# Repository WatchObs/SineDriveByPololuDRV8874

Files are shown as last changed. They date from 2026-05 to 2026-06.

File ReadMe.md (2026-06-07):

Stepper motor driver using two DRV8874 Pololu assemblies for direct and FOC control, AS5047D magnetic position sensing assembly and RS485 assembly. Teensy 4.0 via Arduino IDE to code control of these assemblies. 
The emphasis is control of a Right Ascension axis of an equatorial telescope as the original Makerbase Servo57D did not allow for reducing a rythmic 1+ arcsec variation due to motor pole differences as Makerbase does not provide open sources or access to the processor. In sidereal and pulse tracking mode, direct current control (D axis in D-Q rotor frame of reference) is used as FOC at the 0.25 RPM does not allow sufficient finesse (the stepper is driving a worm directly that drives a 360 tooth gear, 0.25 RPM equates to sidereal), and FOC for slewing.

The board mounted on the back of a Nema 23 stepper for the AS5047D, or if an external (glass type) ABI encoder is used, jumpers provide that programmation.

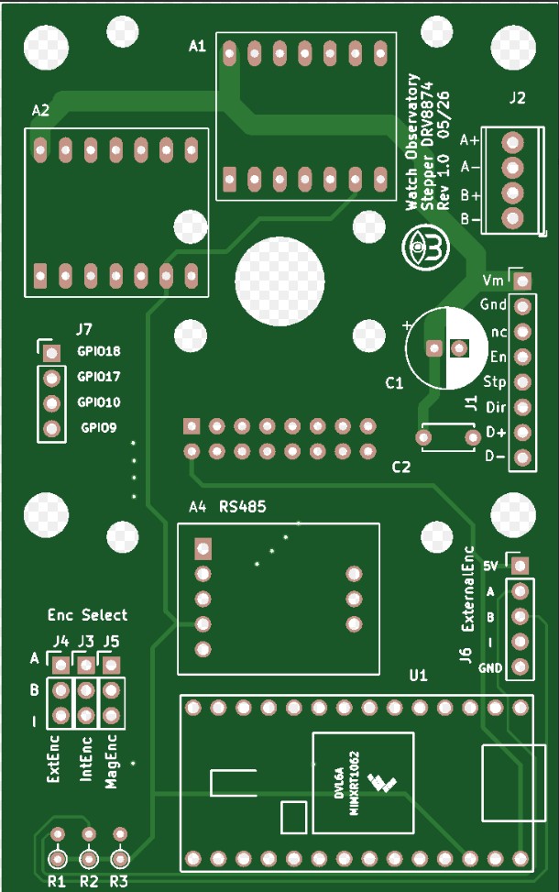
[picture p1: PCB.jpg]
Description

DRV8874Stepper

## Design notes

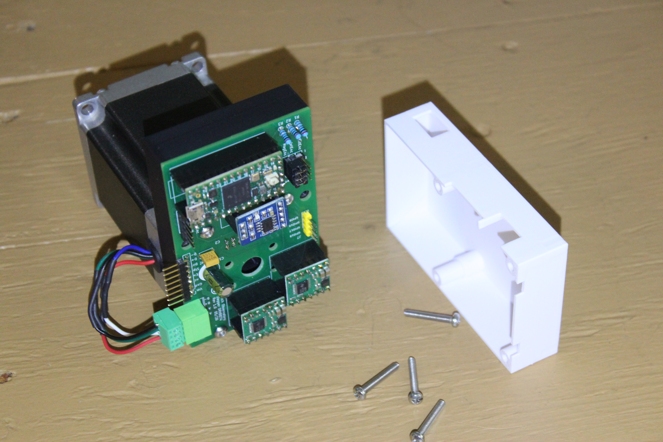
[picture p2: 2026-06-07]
DRV8874Stepper.jpg

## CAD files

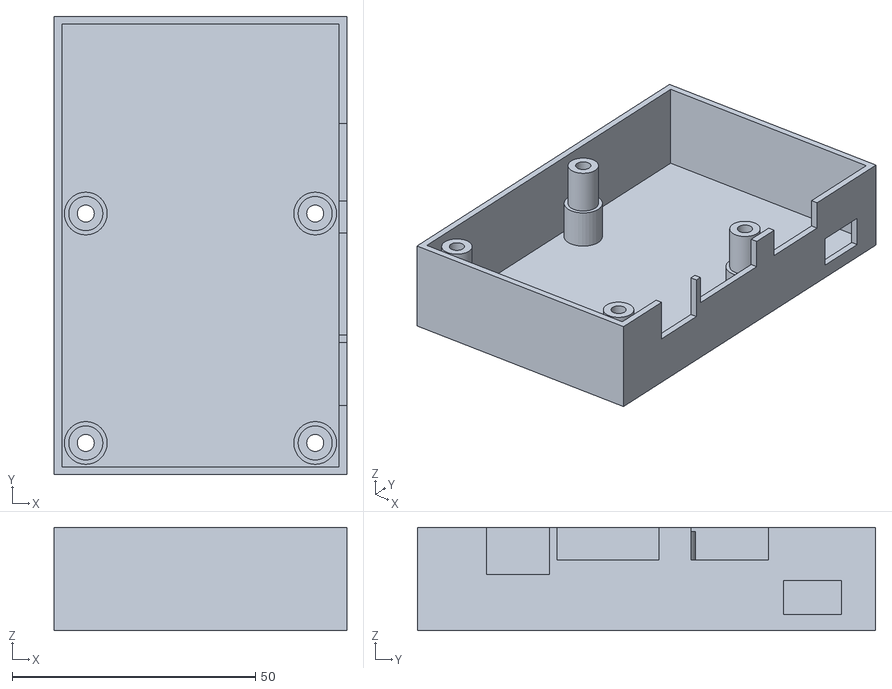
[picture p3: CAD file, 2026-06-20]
Nema23DRV8824 StandAloneCover.stl
60.2 x 94.2 x 21.2

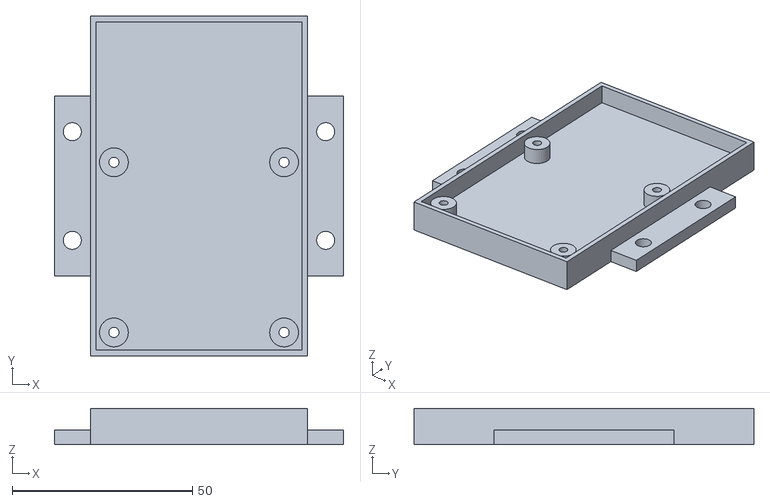
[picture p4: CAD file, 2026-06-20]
Nema23DRV8824 StandAloneBase.stl
80.2 x 94.2 x 10.0

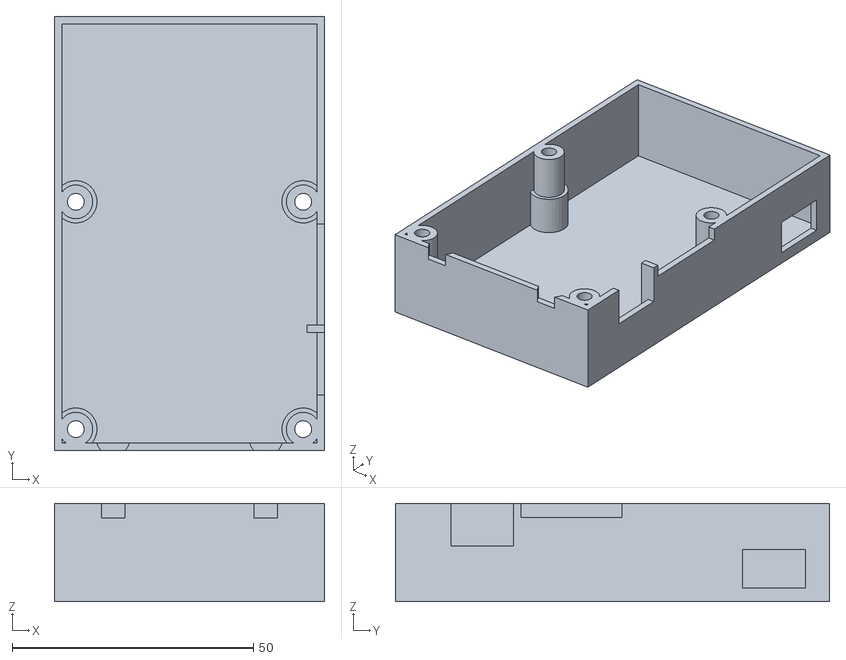
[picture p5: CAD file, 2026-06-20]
Nema23DRV8824.stl
56.0 x 90.0 x 20.4

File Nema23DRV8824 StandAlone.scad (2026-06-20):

//////////////////////////////////////////////////////////////
// Standalone Base + cover 
// DRV8874 based driver - AS5074D or ABI glass encoder
//////////////////////////////////////////////////////////////

$fn = 180;

DoCover = 1;
DoBase  = 0;

// ------------------------------------------------------------
// Motor rear pattern
// ------------------------------------------------------------
bolt_spacing_x   = 31.7;
bolt_spacing_y   = 51.0;
bolt_hole_dia    = 3.5;
nema23_spacing   = 47.14;

// ------------------------------------------------------------
// mainPCBboard standoffs
// ------------------------------------------------------------
mainPCB_w           = nema23_spacing;
mainPCB_h           = nema23_spacing;
mainPCB_standoff_h  = 5; //9.24;
mainPCB_hole_offset = 0;
mainPCBWall         = 1.6;
mainPCBLip          = 0;

post_dia         = 8.0;
post_hole_dia    = 2.8;

// ------------------------------------------------------------
// Base plate geometry
// ------------------------------------------------------------
plate_w          = 56+2*mainPCBWall+1;
plate_h          = 90+2*mainPCBWall+1;
plate_thickness  = 4;

// ------------------------------------------------------------
// Cover geometry
// ------------------------------------------------------------
coverHeight      = 18 + mainPCBWall;
cover_internal_h = 25;
cover_wall       = 2.0;
cover_clearance  = 0.3;
cover_narrow     = 1.0;
cover_offset_x   = plate_w + 20;

//////////////////////////////////////////////////////////////
// Base plate
//////////////////////////////////////////////////////////////
module base_plate() 
{
 difference() 
 {
  // Plate + your tab thickener block
  union() 
  {
   translate([-plate_w/2, -plate_w/2, 0])
    cube([plate_w, plate_h, plate_thickness]);

   // Wall
   translate([0, plate_h/2-plate_w/2, plate_thickness+mainPCB_standoff_h/2])
    difference()
    {
      cube([plate_w,plate_h,mainPCB_standoff_h+mainPCBLip],center=true);
      cube([plate_w-mainPCBWall*2,plate_h-mainPCBWall*2,mainPCB_standoff_h+mainPCBLip],center=true);
    }
  }
 }
  // Mounting tabs
 TabW  = 10;
 TabL  = 50;
 BaseW = plate_w+2*TabW;
 BaseH = plate_h;
 translate([-BaseW/2, plate_h/2-plate_w/2-TabL/2, 0])
  difference()
  {
   cube([BaseW, TabL, plate_thickness]);
   for (y = [-plate_w/4, plate_w/4])
    for (x = [-(BaseW-TabW)/2, (BaseW-TabW)/2])
    {
     translate([x+BaseW/2,TabL/2+y,-5])
      cylinder(h=10,d=5);
    }
  }
}

//////////////////////////////////////////////////////////////
// mainPCBboard standoffs
//////////////////////////////////////////////////////////////
module mainPCBboard_standoffs(drill = 0) 
{
 for (x = [-mainPCB_w/2 + mainPCB_hole_offset, mainPCB_w/2 - mainPCB_hole_offset])
  for (y = [-mainPCB_h/2 + mainPCB_hole_offset, mainPCB_h/2 - mainPCB_hole_offset])
  {
   if (drill)
   {
    translate([x, y, -100])            cylinder(d=post_hole_dia, h=200, $fn=32);
   }
   else
   {
    difference() 
    {
     translate([x, y, plate_thickness]) cylinder(d=post_dia, h=mainPCB_standoff_h, $fn=32);
     translate([x, y, -100])            cylinder(d=post_hole_dia, h=200, $fn=32);
    }
   }
  }
}

module cover() 
{
 postDiaL = 7.0;
 postDiaU = 8.8;
 postDiaIL = 3.5;
 postDiaIU = 6.5;
 postDepthU=coverHeight-10;

 difference() 
 {
  // Plate 
  union() 
  {
   translate([-plate_w/2, -plate_w/2, 0]) cube([plate_w, plate_h, mainPCBWall]);
   
   // Wall
   translate([0, plate_h/2-plate_w/2, coverHeight/2+mainPCBWall-mainPCBLip/2])
   difference()
   {
    cube([plate_w,plate_h,coverHeight-mainPCBLip],center=true);
    cube([plate_w-mainPCBWall*2,plate_h-mainPCBWall*2,coverHeight*1.1-mainPCBLip],center=true);
   }

   // Retainer bolts posts & well (body)
   for (x = [-mainPCB_w/2 + mainPCB_hole_offset, mainPCB_w/2 - mainPCB_hole_offset])
    for (y = [-mainPCB_h/2 + mainPCB_hole_offset, mainPCB_h/2 - mainPCB_hole_offset]) 
    {
     translate([x, y, mainPCBWall/2]) cylinder(d=postDiaL, h=coverHeight);
     translate([x, y, mainPCBWall/2]) cylinder(d=postDiaU, h=postDepthU, $fn=32);
    }
    // Host connector post (strength)
//    translate([plate_w/2-mainPCBWall-2,-plate_w/2+29-0.75,mainPCBWall/2]) 
//     cube([2,1.5,coverHeight-mainPCBLip/2-.2]);
  }

  // Retainer bolts posts & well (holes)
  for (x = [-mainPCB_w/2 + mainPCB_hole_offset, mainPCB_w/2 - mainPCB_hole_offset])
   for (y = [-mainPCB_h/2 + mainPCB_hole_offset, mainPCB_h/2 - mainPCB_hole_offset]) 
   {
    translate([x, y, -5]) cylinder(d=postDiaIL, h=30, $fn=32);
    translate([x, y, 0])  cylinder(d=postDiaIU, h=postDepthU-2, $fn=32);
   }
   translate([0,(2*mainPCBWall-.5),-mainPCBLip/2])
   {
    // Motor connector
    translate([plate_w/2-4,-plate_w/2+11.5,coverHeight+mainPCBWall/2-9+.1])
     cube([6,13,12]);
    // Host connector
    translate([plate_w/2-4,-plate_w/2+26,coverHeight+mainPCBWall/2-6+.1])
     cube([6,21,8]);
    // Encoder connector
    translate([plate_w/2-4,-plate_w/2+26+6+21.5,coverHeight+mainPCBWall/2-6+.1])
     cube([6,16,8]);
    // USB connector
    translate([plate_w/2-4,-plate_w/2+67.5+10/2,coverHeight+mainPCBWall/2-5/2-14.7+.1])
     cube([6,12,7]);
   }
 } // Difference
}

//////////////////////////////////////////////////////////////
// Final assembly
//////////////////////////////////////////////////////////////
union()
{
 if (DoBase)
 {
  difference()
  {
   base_plate();
   mainPCBboard_standoffs(1);
  }
  mainPCBboard_standoffs(0);
 }

 if (DoCover) 
 {
  translate([100,0,0]) cover();
 }
}

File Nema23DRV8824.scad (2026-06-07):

//////////////////////////////////////////////////////////////
// Servo57D Rear Mount Plate + Snap-On Cover (offset)
// DRV8874 based driver board replaces Makerbase driver
// Literal T-cutout + 4  holes + recess for board slide-up
//////////////////////////////////////////////////////////////

$fn = 180;

DoCover = 1;
DoBase  = 0;

// ------------------------------------------------------------
// Motor rear pattern
// ------------------------------------------------------------
bolt_spacing_x   = 31.7;
bolt_spacing_y   = 51.0;
bolt_hole_dia    = 3.5;
nema23_spacing   = 47.14;

// ------------------------------------------------------------
// Base plate geometry
// ------------------------------------------------------------
plate_w          = 56;
plate_h          = 90;
plate_thickness  = 6;

// ------------------------------------------------------------
// Snap-on cover groove
// ------------------------------------------------------------
groove_offset    = 1.5;
groove_height    = 1.5;
groove_depth     = 1.0;

groove_top       = plate_thickness - groove_offset;
groove_bottom    = groove_top - groove_height;

// ------------------------------------------------------------
// Literal T-cutout dimensions
// ------------------------------------------------------------
stem_w = 11;
stem_h = 17;

T_top_w = 24;
T_top_h = 12;

// Side region width (tabs)
side_w = (T_top_w - stem_w) / 2;

// PCB hole spacing
m1_d = 1.8;
hole_dy = 11/2;

// Recess depth for board slide-up
recess_depth = 4.33;

// ------------------------------------------------------------
// mainPCBboard standoffs
// ------------------------------------------------------------
mainPCB_w           = nema23_spacing;
mainPCB_h           = nema23_spacing;
mainPCB_standoff_h  = 9.24;
mainPCB_hole_offset = 0;
mainPCBWall         = 1.6;

post_dia         = 8.0;
post_hole_dia    = 2.8;

// ------------------------------------------------------------
// Cover geometry
// ------------------------------------------------------------
coverHeight = 18+mainPCBWall;
cover_internal_h = 25;
cover_wall       = 2.0;
cover_clearance  = 0.3;
cover_narrow     = 1.0;

rib_height       = groove_height;
rib_depth        = groove_depth * 0.9;

cover_offset_x   = plate_w + 20;

//////////////////////////////////////////////////////////////
// Literal T-shaped through-cut
//////////////////////////////////////////////////////////////
module encoder_T_cutout() {

    translate([-stem_w/2, -stem_h/2, -0.1])
        cube([stem_w, stem_h, plate_thickness + 10]);

    translate([-T_top_w/2, stem_h/2, -0.1])
        cube([T_top_w, T_top_h, plate_thickness + 10]);
}

//////////////////////////////////////////////////////////////
// PCB holes
//////////////////////////////////////////////////////////////
module pcb_bolt_holes() {

    x_left  = -(stem_w/2 + side_w/2);
    x_right =  (stem_w/2 + side_w/2);

    for (x = [x_left, x_right])
    for (y = [-hole_dy, hole_dy])
        translate([x, y, -0.1])
            cylinder(d=m1_d, h=plate_thickness + 10);
}

//////////////////////////////////////////////////////////////
// Recess under side regions
//////////////////////////////////////////////////////////////
module encoder_recess() {

    translate([-(stem_w/2 + side_w), -stem_h/2, 0])
        cube([side_w, stem_h, recess_depth]);

    translate([stem_w/2, -stem_h/2, 0])
        cube([side_w, stem_h, recess_depth]);
}

//////////////////////////////////////////////////////////////
// Triangular groove profile (horizontal wedge)
//////////////////////////////////////////////////////////////
module tri_xz() {
    polygon(points = [
        [0, 0],                 // outer bottom
        [groove_depth, groove_height/2],      // inner bottom
        [0, groove_height]      // vertex inward
    ]);
}

//////////////////////////////////////////////////////////////
// Base plate
//////////////////////////////////////////////////////////////
module base_plate() {
    difference() {

        // Plate + your tab thickener block
        union() {
            translate([0,-1,plate_thickness])
                cube([T_top_w+4, stem_h+2, 4],center=true);

            translate([-plate_w/2, -plate_w/2, 0])
                cube([plate_w, plate_h, plate_thickness]);

            // Wall
            translate([0, plate_h/2-plate_w/2, plate_thickness+mainPCB_standoff_h/2])
            difference()
            {
              cube([plate_w,plate_h,mainPCB_standoff_h],center=true);
              cube([plate_w-mainPCBWall*2,plate_h-mainPCBWall*2,mainPCB_standoff_h],center=true);
            }
        }

        // Motor bolt holes
        for (x = [-bolt_spacing_x/2, bolt_spacing_x/2])
        for (y = [-bolt_spacing_y/2, bolt_spacing_y/2])
            translate([x, y, -0.1])
                cylinder(d=bolt_hole_dia, h=plate_thickness + 10);

        // Literal T-cutout
        encoder_T_cutout();

        // PCB holes
        pcb_bolt_holes();

        // Recess
        encoder_recess();

        // ------------------------------------------------------------
        // Triangular perimeter grooves (correctly rotated)
        // ------------------------------------------------------------

//        // LEFT side (extrude along Y)
//        translate([-plate_w/2, -plate_h/2, groove_bottom])
//            rotate([-90,0,0])
//            linear_extrude(height = plate_h)
//                tri_xz();

//        // RIGHT side (mirror X)
//        translate([plate_w/2, -plate_h/2, groove_bottom])
//            rotate([-90,0,0])
//            mirror([1,0,0])
//                linear_extrude(height = plate_h)
//                    tri_xz();

//        // BOTTOM side (rotate 90°)
//        translate([plate_w/2, -plate_h/2, groove_bottom])
//            rotate([-90,0,90])
//                linear_extrude(height = plate_w)
//                    tri_xz();

//        // TOP side (rotate -90°)
//        translate([-plate_w/2, plate_h/2, groove_bottom])
//            rotate([-90,0,-90])
//                linear_extrude(height = plate_w)
//                    tri_xz();
    }
}

//////////////////////////////////////////////////////////////
// mainPCBboard standoffs
//////////////////////////////////////////////////////////////
module mainPCBboard_standoffs() {

    for (x = [-mainPCB_w/2 + mainPCB_hole_offset, mainPCB_w/2 - mainPCB_hole_offset])
    for (y = [-mainPCB_h/2 + mainPCB_hole_offset, mainPCB_h/2 - mainPCB_hole_offset]) {

        difference() {
            translate([x, y, plate_thickness])
                cylinder(d=post_dia, h=mainPCB_standoff_h, $fn=32);

            translate([x, y, -100])
                cylinder(d=post_hole_dia, h=200, $fn=32);
        }
    }
    
}

//////////////////////////////////////////////////////////////
// Cover (unchanged)
//////////////////////////////////////////////////////////////
module rib_xz() {
    polygon(points = [
        [0, 0],
        [rib_depth, 0],
        [0, rib_height]
    ]);
}

//////////////////////////////////////////////////////////////
// Cover ribs: same isosceles profile + matching rotations
//////////////////////////////////////////////////////////////
module rib_xz() {
    polygon(points = [
        [0, 0],
        [rib_depth, rib_height/2],
        [0, rib_height]
    ]);
}

//////////////////////////////////////////////////////////////
// Cover ribs: same isosceles profile + correct rotations
//////////////////////////////////////////////////////////////
module rib_xz() {
    polygon(points = [
        [0, 0],
        [rib_depth, rib_height/2],
        [0, rib_height]
    ]);
}

module cover() {
postDiaL = 7.0;
postDiaU = 8.8;
postDiaIL = 3.5;
postDiaIU = 6.5;
postDepthU=coverHeight-10;


    difference() {

        // Plate 
        union() 
        {

         translate([-plate_w/2, -plate_w/2, 0]) cube([plate_w, plate_h, mainPCBWall]);

         // Wall
         translate([0, plate_h/2-plate_w/2, coverHeight/2+mainPCBWall/2])
         difference()
         {
           cube([plate_w,plate_h,coverHeight],center=true);
           cube([plate_w-mainPCBWall*2,plate_h-mainPCBWall*2,coverHeight*1.1],center=true);
         }

         // Retainer bolts posts & well (body)
         for (x = [-mainPCB_w/2 + mainPCB_hole_offset, mainPCB_w/2 - mainPCB_hole_offset])
           for (y = [-mainPCB_h/2 + mainPCB_hole_offset, mainPCB_h/2 - mainPCB_hole_offset]) 
           {
             translate([x, y, mainPCBWall/2]) cylinder(d=postDiaL, h=coverHeight,   $fn=32);
             translate([x, y, mainPCBWall/2]) cylinder(d=postDiaU, h=postDepthU, $fn=32);
           }
         // Host connector post (strength)
         translate([plate_w/2-mainPCBWall-2,-plate_w/2+26-1.5,mainPCBWall/2]) cube([2,1.5,coverHeight]);
       }
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

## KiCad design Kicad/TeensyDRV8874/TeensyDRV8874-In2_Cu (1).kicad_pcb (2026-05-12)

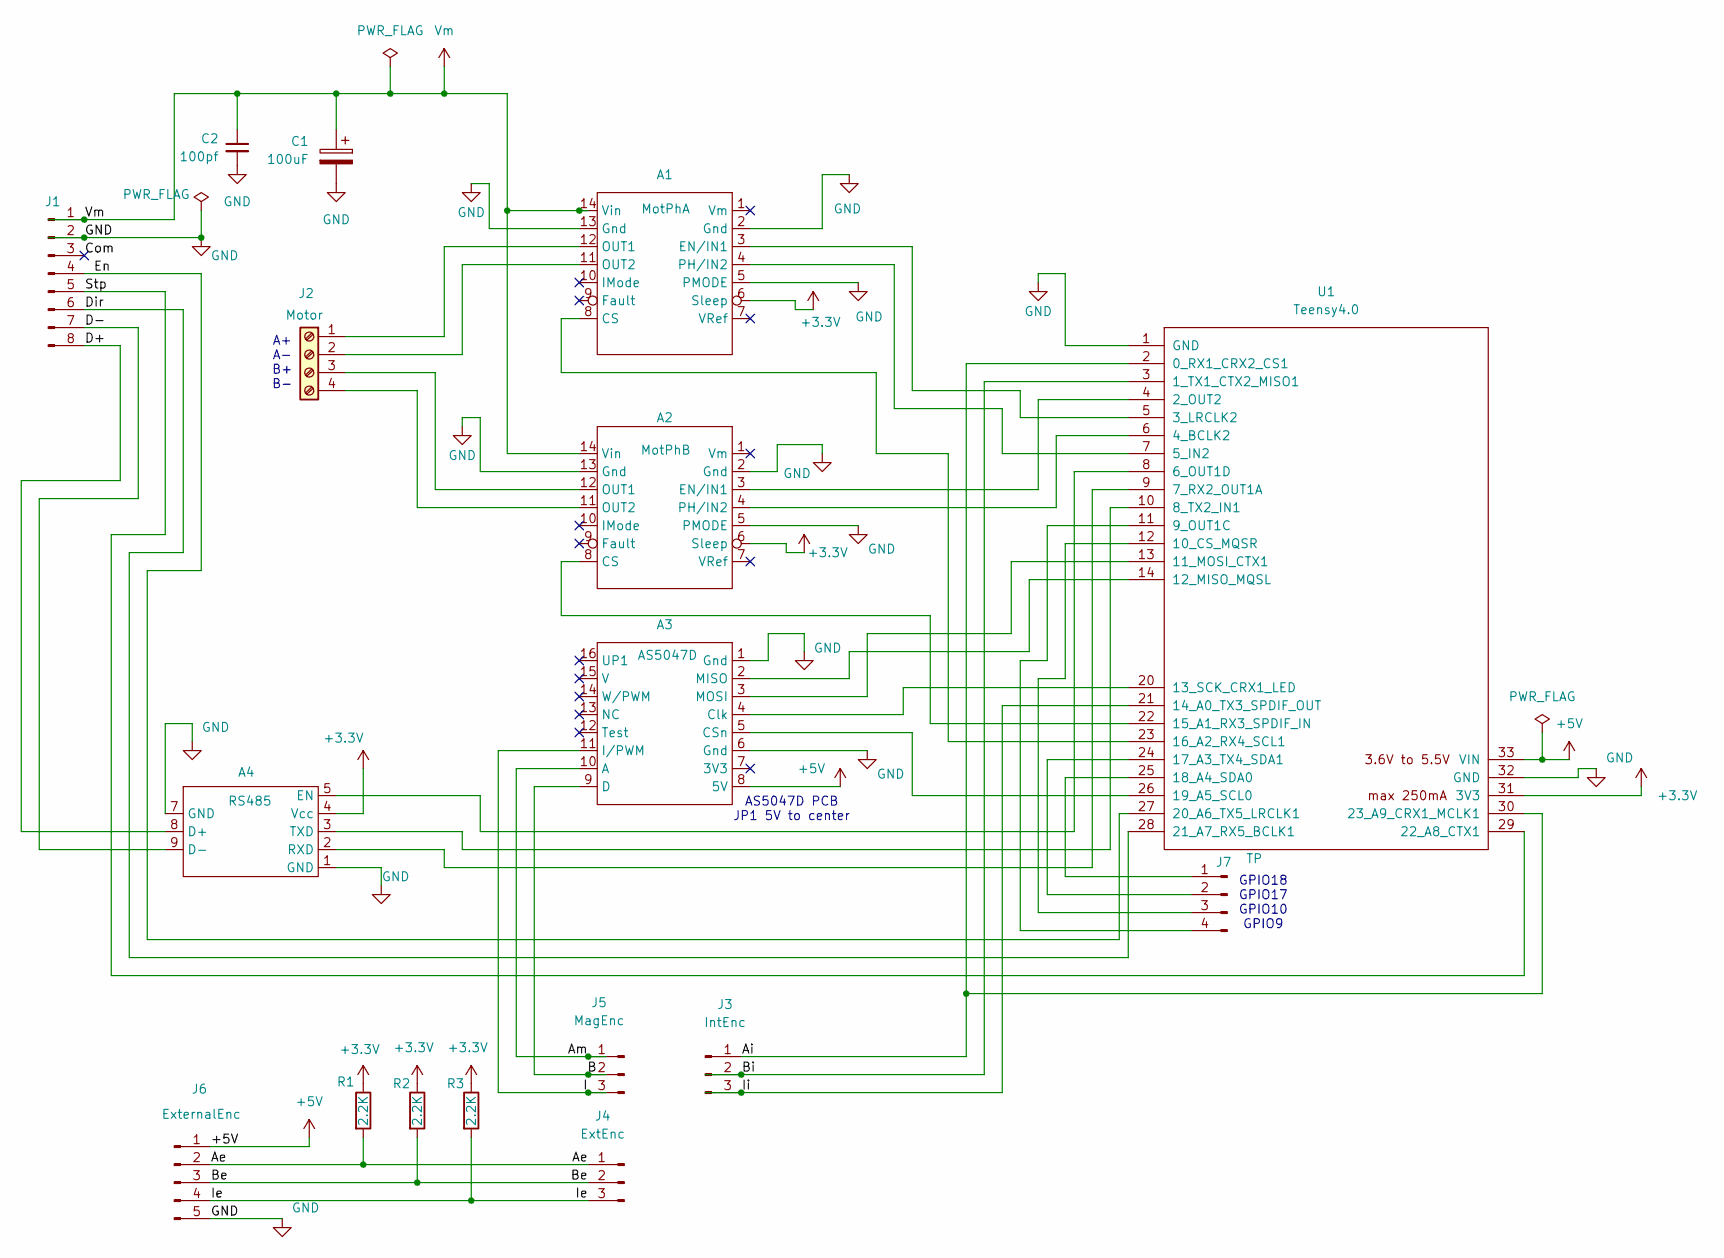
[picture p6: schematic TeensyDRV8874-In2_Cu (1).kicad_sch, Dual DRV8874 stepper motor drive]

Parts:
A1: MotPhA; DRV8874
A2: MotPhB; DRV8874
A3: AS5047D
A4: RS485
C1: 100uF; CP_Radial_D8.0mm_P2.50mm
C2: 100pf; C_Disc_D5.0mm_W2.5mm_P5.00mm
J1: PinHeader_1x08_P2.54mm_Vertical
J2: Motor; TerminalBlock-1x04_P2.54mm_Horizontal
J3: IntEnc; PinHeader_1x03_P2.54mm_Vertical
J4: ExtEnc; PinHeader_1x03_P2.54mm_Vertical
J5: MagEnc; PinHeader_1x03_P2.54mm_Vertical
J6: ExternalEnc; PinHeader_1x05_P2.54mm_Vertical
J7: TP; PinHeader_1x04_P2.54mm_Vertical
R1, R2, R3: 2.2K; R_Axial_DIN0204_L3.6mm_D1.6mm_P2.54mm_Vertical
U1: Teensy4.0; Teensy40

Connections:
+3.3V: A1.6 (Sleep), A2.6 (Sleep), A4.4 (Vcc), R1.1, R2.1, R3.1, U1.31 (3V3)
+5V: A3.8 (5V), J6.1 (+5V), U1.33 (VIN)
/Ae: J4.1 (Ae), J6.2 (Ae), R1.2
/Ai: J3.1 (Ai), U1.2 (0_RX1_CRX2_CS1), U1.30 (23_A9_CRX1_MCLK1)
/Am: A3.10 (A), J5.1 (Am)
/B: A3.9 (D), J5.2 (Bm)
/Be: J4.2 (Be), J6.3 (Be), R2.2
/Bi: J3.2 (Bi), U1.3 (1_TX1_CTX2_MISO1)
/Com: J1.3 (Com)
/D+: A4.8 (D+), J1.8 (D+)
/D-: A4.9 (D-), J1.7 (D-)
/Dir: J1.6 (Dir), U1.28 (21_A7_RX5_BCLK1)
/En: J1.4 (En), U1.27 (20_A6_TX5_LRCLK1)
/I: A3.11 (I/PWM), J5.3 (Im)
/Ie: J4.3 (Ie), J6.4 (Ie), R3.2
/Ii: J3.3 (Ii), U1.21 (14_A0_TX3_SPDIF_OUT)
/Stp: J1.5 (Stp), U1.29 (22_A8_CTX1)
GND: A1.2 (Gnd), A1.5 (PMODE), A1.13 (Gnd), A2.2 (Gnd), A2.5 (PMODE), A2.13 (Gnd), A3.1 (Gnd), A3.6 (Gnd), A4.1 (GND), A4.7 (GND), C1.2, C2.2, J1.2 (GND), J6.5 (GND), U1.1 (GND), U1.32 (GND)
unnamed: A1.8 (CS), U1.23 (16_A2_RX4_SCL1)
unnamed: A1.3 (EN/IN1), U1.5 (3_LRCLK2)
unnamed: A1.12 (OUT1), J2.1 (A+)
unnamed: A1.11 (OUT2), J2.2 (A-)
unnamed: A1.4 (PH/IN2), U1.7 (5_IN2)
unnamed: A2.8 (CS), U1.22 (15_A1_RX3_SPDIF_IN)
unnamed: A2.3 (EN/IN1), U1.4 (2_OUT2)
unnamed: A2.12 (OUT1), J2.3 (B+)
unnamed: A2.11 (OUT2), J2.4 (B-)
unnamed: A2.4 (PH/IN2), U1.6 (4_BCLK2)
unnamed: A3.5 (CSn), U1.26 (19_A5_SCL0)
unnamed: A3.4 (Clk), U1.20 (13_SCK_CRX1_LED)
unnamed: A3.2 (MISO), U1.14 (12_MISO_MQSL)
unnamed: A3.3 (MOSI), U1.13 (11_MOSI_CTX1)
unnamed: A4.5 (EN), U1.8 (6_OUT1D)
unnamed: A4.2 (RXD), U1.9 (7_RX2_OUT1A)
unnamed: A4.3 (TXD), U1.10 (8_TX2_IN1)
unnamed: J7.1, U1.25 (18_A4_SDA0)
unnamed: J7.2, U1.24 (17_A3_TX4_SDA1)
unnamed: J7.3, U1.12 (10_CS_MQSR)
unnamed: J7.4, U1.11 (9_OUT1C)
Vm: A1.14 (Vin), A2.14 (Vin), C1.1, C2.1, J1.1 (+15V)

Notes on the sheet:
GPIO18 GPIO17 GPIO10 GPIO9
AS5047D PCB JP1 5V to center
A+ A- B+ B-

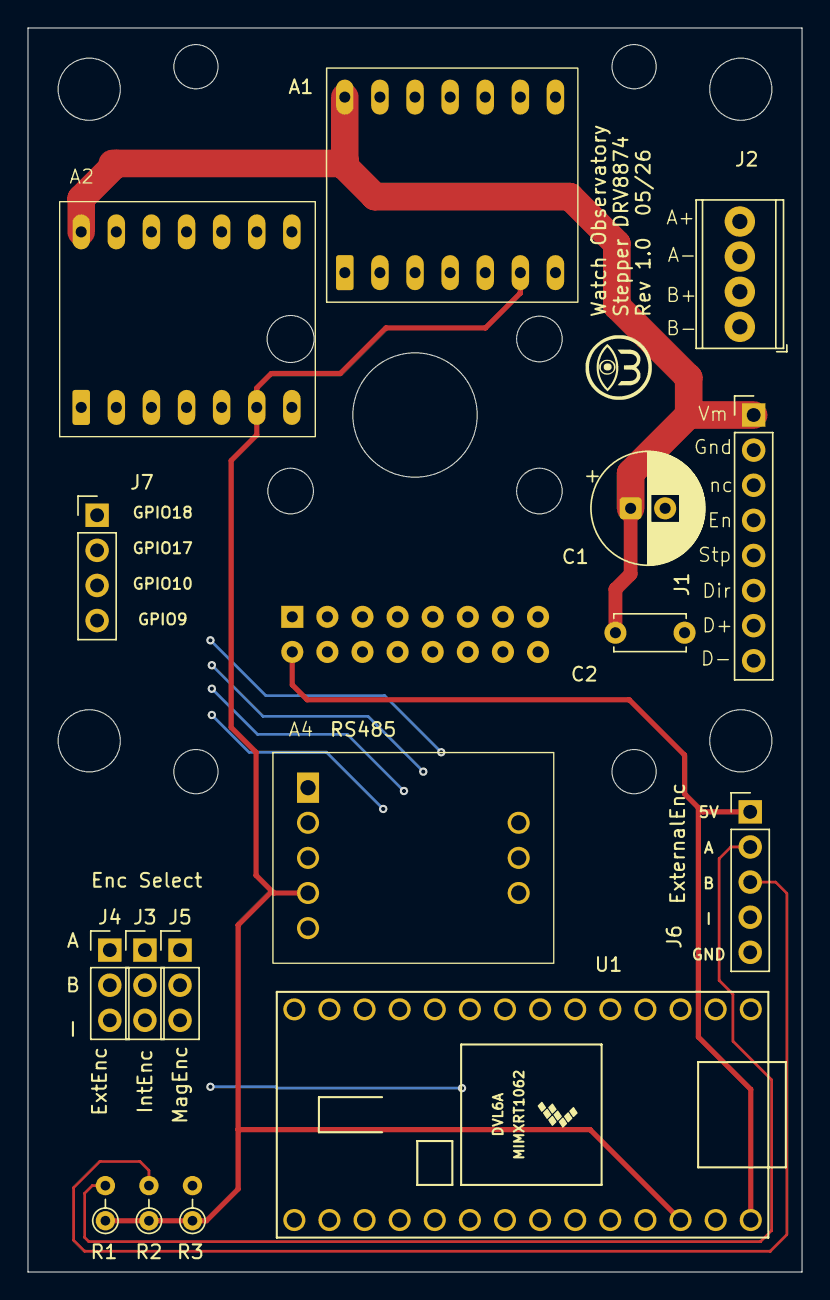
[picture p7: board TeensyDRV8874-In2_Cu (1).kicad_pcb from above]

Board: 4 copper layers, 56.0 x 90.0 mm, 18 parts (1 on the bottom side), 39 nets.

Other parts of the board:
Nema23: MountingHole_4.5mm

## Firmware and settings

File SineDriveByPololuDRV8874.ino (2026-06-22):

/*
  Sinusoidal micro stepper with loss-of-pulses safety
  - External STEP on pin 21 used only for measurement (freq)
  - ISR integrates published host rate (indices per ISR) into a float phase accumulator
  - If no STEP edges seen for LOSS_TIMEOUT_MS, published rate is forced to zero
*/

#include <Arduino.h>
#include <stdint.h>
#include <math.h>
#include <FreqMeasureMulti.h>
#include <Encoder.h>
#include <SPI.h>

// --- Host step loss timeout ---
const uint32_t LOSS_TIMEOUT_MS = 500;   // adjust as needed
volatile uint32_t lastHostStepTime = 0;
volatile bool hostTimedOut = false;

volatile float fMax = 0.f;
volatile float fMin = 0.f;

// Pins
const int PIN_A_PH         = 5;   // Phase (direction) for winding A
const int PIN_A_EN         = 3;   // Enable (PWM) for winding A
const int PIN_B_PH         = 4;   // Phase (direction) for winding B
const int PIN_B_EN         = 2;   // Enable (PWM) for winding B
const int PIN_CS_A         = 16;  // DRV8874 CS for winding A - current sensing
const int PIN_CS_B         = 15;  // DRV8874 CS for winding B - current sensing

const int PIN_ENC_A        = 0;   // Encoder Quadrature A
const int PIN_ENC_B        = 1;   // Encoder Quadrature B
const int PIN_ENC_IDX      = 14;  // Encoder Index (Z)  [was 12 with disk encoder]
const int PIN_ENC_RATE     = 23;  // Measure encoder pulse rate (phase A) - pairs with 22
const int PIN_ENC_MOSI     = 11;  // Encoder comm (SPI0 - define here only to lock pin from being used)
const int PIN_ENC_MISO     = 12;  // Encoder comm (SPI0 - define here only to lock pin from being used)
const int PIN_ENC_SCK      = 13;  // Encoder comm (SPI0 - define here only to lock pin from being used)

const int PIN_HOST_ENABLE  = 20;  // Host motor enable DIP
const int PIN_HOST_DIR     = 21;  // Host motor direction DIP
const int PIN_HOST_RATE    = 22;  // Host requested rate (freq) - pairs with 23

const int PIN_RX2          = 7;   // RS485 receive comm with host
const int PIN_TX2          = 8;   // RS485 transmit comm with host
const int PIN_DE_RE        = 6;   // RS485 bus enable

const int PIN_ISR_TOGGLE   = 10;  // Debug - ISR active signal (monitor CPU usage by ISR)
const int PIN_RATE_PWM     = 9;   // Debug - local motor rate
const int PIN_LED          = 13;  // On-board LED (also SPI SCK)

const int PIN_ENC_CS       = 19;  // AS5047D chip select (CSn)

const uint32_t RS485_BAUD = 115200; // RS485 host comm baud rate

// Waveform / motor geometry
const int   BPWM_FREQ       = 25000;          // PWM frequency for DRV8874 driver
const uint32_t uStepPerTurn = 51200;          // Microsteps per revolution
const float maxFreq         = uStepPerTurn*5; // Maximum frequency (set according P/S & stepper specs)
const float transFreqHz     = uStepPerTurn/2; // Frequency for drive mode transition
const int   PWM_BITS        = 12;             // PWM resolution
const float PWM_MAG         = (float)(pow(2, PWM_BITS)-0); // PWM magnitude
#define MAG_CYCLES_PER_REV  50                // Electrical cycles per mechanical revolution
#define CAL_CNT MAG_CYCLES_PER_REV            // AS5074D calibration indexes

const uint32_t RATE_PWM_FREQ_HZ = uStepPerTurn*5; // Debug - FOR TESTING

// ISR timing
const uint32_t ISR_FREQ_HZ   = 25000UL;                 // ISR ticks per second
const uint32_t ISR_PERIOD_US = 1000000UL / ISR_FREQ_HZ; // dt in uSec
const float    ISR_DT        = 1.f/(float)ISR_FREQ_HZ;  // dt in sec
volatile float isrTmUs       = 0.f;                     // ISR run time micro seconds

// Host rate steps/sec conversion to magnetic phase
const float rateToDeg  = 360.f/(float)uStepPerTurn;

// ADC
const int ADC_BITS = 12;

// AS5047D uses SPI MODE1, up to 10 MHz
SPISettings encSPI(10000000, MSBFIRST, SPI_MODE1);

// --- Shared state (volatile for ISR/main) ---
volatile double cmdDeg        = 0.0f;   // Commanded shaft angle (degrees) fine resolution due to ISR dt integration at low slew rates
volatile float  phaseAdv      = 0.0f;   // Phase advance
volatile float  pE            = 0.0f;   // Position error
volatile float  pEI           = 0.0f;   // Position error integration
volatile float  vE            = 0.0f;   // Velocity error
volatile float  vEI           = 0.0f;   // Velocity error integration
volatile float  vdE           = 0.0f;   // I2V D axis error
volatile float  vdEI          = 0.0f;   // I2V D axis error integration
volatile float  vqE           = 0.0f;   // I2V Q axis error
volatile float  vqEI          = 0.0f;   // I2V Q axis error integration
volatile float  dirSign       = 1;      // +1 CW, -1 CCW
volatile int8_t enableDrv     = HIGH;   // Drive enable
volatile int    releaseForUse = 0;      // Stepper released for normal drive
volatile float  freqMeasureHz = 0.f;    // Host step frequency

volatile int   isrCount = 0;

FreqMeasureMulti FreqMeasure1;          // Measure host step rate
FreqMeasureMulti FreqMeasure2;          // Measure encoder phase A rate

// Slew-limited output frequency for phase integration
volatile float slewFreqHz = 0.f;        // deg/sec
const float SLEW_RATE_HZ_PER_ISR = (float)uStepPerTurn * 5.f / (float)ISR_FREQ_HZ;

// Driver motor currents
#define MAX_CURR       2.1f  // Max current limit DRV8824 (continuous)
#define SUP_VOLT      15.f   // Supply voltage
#define PHASE_ADV      5.f   // Phase advance per 360 deg/sec motor velocity
#define PHASE_ADV_MAX 30.f   // Maximum permissible phase advance
#define DIRECT_CURR   1.5f   // Direct mode target current (d axis)
// 15V supply, 4.8 mH, 1.13 ohms, 23HS30-2804D StepperOnline nema 23
// 15V supply, 3.0 mH, 1.00 ohms, 57BYGH633 Servo57D stepper Nema 23
#define V_KP          0.5f   // Proportional voltage gain (normalized)
#define V_KI          2.0f   // Integral voltage gain (normalized)
#define SERVO_KP      0.7f   // Position error gain (was 2 with external 00ppr encoder)
#define SERVO_KPI     0.2f   // Integrated position error gain
#define SERVO_KV    0.002f   // Velocity error gain
#define SERVO_KVI    0.01f   // Integrated velocity error gain
const    float convCS = (3.3f/(float)pow(2,ADC_BITS)) * (1.0f/1.1f); // CS scaling: 1.1V/A
volatile float Ia    = 0.f;  // Motor coil current A
volatile float Ib    = 0.f;  // Motor coil current B
volatile float Id    = 0.f;  // Rotor frame current - D axis
volatile float Iq    = 0.f;  // Rotor frame current - Q axis
volatile float IqDem = 0.f;  // Rotor frame demanded current - Q axis
volatile float IaPol = 1.f;  // Polarity of current A
volatile float IbPol = 1.f;  // Polarity of current B
volatile float Va    = 0.f;  // Duty cycle phase A
volatile float Vb    = 0.f;  // Duty cycle phase 
volatile float Vd    = 0.f;  // Duty cycle D 
volatile float Vq    = 0.f;  // Duty cycle Q
volatile float IdReq = DIRECT_CURR; // Rotor frame 0 D axis requested current

#define USE_EXT_ENC  1  // Use external encoder (ABI) otherwise AS5074D SPI magnetic position 14 bits

#if (USE_EXT_ENC)
#define ENC_REZ             2500  // Encoder counts per turn either phase - glass external encoder
#define CAL_ENC_REZ (ENC_REZ *4)  // Encoder rez for calibration
#else
#define ENC_REZ              512  // Encoder counts per turn either phase - AS5074D ABI default boot up value (and max)
#define CAL_ENC_REZ    (1 << 14)  // Encoder rez for calibration 
#endif
#define ENC_QUAD_REZ (ENC_REZ * 4)// Encoder quadrature counts per turn
#define CAL_NONE               0  // AS5074D calibration not done
#define CAL_LEARN              1  // AS5074D calibration learn (sweeping)
#define CAL_DONE               2  // AS5074D calibration learn completed
#define CAL_VALID              3  // AS5074D calibration valid
Encoder motorEncoder(PIN_ENC_A, PIN_ENC_B);
volatile float  motDeg    = 0.f;  // Motor shaft position in degrees
volatile uint16_t magStat = 0;    // AS5074D angle error status bit
volatile uint16_t magRaw  = 0;    // AS5074D 14 bit position + error + parity
volatile uint16_t magDec  = 0;    // AS5074D 14 bit position
volatile float magDeg     = 0;    // AS5074D linearized degrees
volatile float encVel2     = 0.f;  // AS5074D velocity in deg/sec
volatile int   encCalRun  = CAL_NONE; // AS5074D calibration run
volatile int   poleNum    = 0;    // AS5047D calibration run pole number
volatile bool  magBusy    = false;// AS5074D API busy
volatile long  encCnt     = 0;    // Encoder quadrature counts
volatile int   encIndex   = -1;   // Encoder index detection count
volatile float encDeg     = 0.f;  // Encoder shaft angle in degrees
volatile float encOffset  = 0.f;  // Encoder offset (to magnetic cycle)
volatile float encVel     = 0.f;  // Encoder computed velocity from phase A period
volatile float commNrm    = 0.f;  // Commutation angle (normalized)
volatile float commRad    = 0.f;  // Commutation angle (radians)
volatile float magRad     = 0.f;  // Resolved magnetic angle (radians)
volatile float slewRate   = 0.f;  // Motor slew rate deg/sec shaft angle
volatile float motorVel   = 0.f;  // Motor velocity

struct CalibPoint 
{
  int16_t  dec;  // raw encoder position (counts)
  float    deg;  // true mechanical angle (degrees)
  float    m;    // slope
  int      cal;  // calibration flag
};
CalibPoint encCal[CAL_CNT];

#define limit0(A)     (((A)>1.f)   ? 1.f         : (((A)<-1.f)   ? -1.f        : (A)))
#define limit1(A,B)   (((A)<(-B))  ? (-B)        : (((A)> (B))   ?  (B)        : (A)))
#define limit2(A,B,C) (((A)<(B))   ? (B)         : (((A)> (C))   ?  (C)        : (A)))
#define limit180(A)   (((A)>=180.f)? ((A)-360.f) : (((A)<-180.f) ? ((A)+360.f) : (A)))
#define limit360(A)   (((A)>=360.f)? ((A)-360.f) : (((A)<0.f)    ? ((A)+360.f) : (A)))
#define limit360D(A)  (((A)>=360.) ? ((A)-360.)  : (((A)<0.)     ? ((A)+360.)  : (A)))
#define db(A,B)       (((A)>(B))?((A)-(B)):(((A)<-(B))?((A)+(B)):0))
#define hys(A,B,C)    (((A-B)>(C))?(A-C):(((A-B)<-C)?(A+C):B))
#define sign(A)       (((A) < 0)   ? -1   : 1)
#define signf(A)      (((A) < 0.f) ? -1.f : 1.f)

// ---------------------------------------------------------------------------
// Command defines (with parity pre-applied)
// ---------------------------------------------------------------------------
#define CMD_ANGLECOM   0xFFFF // ANGLECOM (0xFFFF) → returns: [15]=parity, [14]=error, [13:0]=angle
#define CMD_ERRFL      0x4001 // read + parity - ERRFL register (0x0001)
#define CMD_STATUS     0x7FFD // read + parity - STATUS register (0x3FFD)
#define CMD_DIAG       0x7FFC // read + parity - DIAAGC register (0x3FFC)
#define AS5047_ANGLE14      0 // 14 bit angle only
#define AS5047_RAW          1 // raw 16‑bit frame (parity + error + angle)
#define AS5047_ERRFL        2 // error flags
#define AS5047_STATUS       3 // status register
#define AS5047_DIAG         4 // diagnostics (AGC + MAG + flags)

uint16_t AS5047_Read(uint16_t what)
{
  uint16_t raw;

  auto spi_xfer = [&](uint16_t cmd) -> uint16_t 
  {
    uint16_t res;
    digitalWrite(PIN_ENC_CS, LOW);
    SPI.beginTransaction(encSPI);
    res = SPI.transfer16(cmd);
    SPI.endTransaction();
    digitalWrite(PIN_ENC_CS, HIGH);
    return res;
  };

  switch (what)
  {
    case AS5047_ANGLE14:
      // Clean 14-bit angle (0–16383)
      raw = spi_xfer(CMD_ANGLECOM);
      return raw & 0x3FFF;

    case AS5047_RAW:
      // Full 16-bit frame:
      // bit15 = parity, bit14 = error, bits13:0 = angle
      return spi_xfer(CMD_ANGLECOM);

    case AS5047_ERRFL:
      // ERRFL bits:
      // bit0 = framing error
      // bit1 = invalid command
      // bit2 = parity error
      // bit3 = diagnostic error
      // bit4 = magnet too strong
      // bit5 = magnet too weak
      // bit6 = CORDIC overflow
      return spi_xfer(CMD_ERRFL);
  
    case AS5047_STATUS:
      // STATUS bits:
      // bit3 = MAGH (mag too strong)
      // bit4 = MAGL (mag too weak)
      // bit5 = COF (CORDIC overflow)
      // bit6 = OCF (offset compensation finished)
      // bit7 = AGC overflow
          return spi_xfer(CMD_STATUS);
    
    case AS5047_DIAG:
      // DIAAGC bits:
      // bits 7:0  = AGC value
      // bits 13:8 = MAG value
      // bit14     = LF  (loss of tracking)
      // bit15     = COF (CORDIC overflow)
      return spi_xfer(CMD_DIAG);
    
    default:
      return 0;
  }
}

void DRV8874(float val, int PIN_PH, int PIN_EN)
{
  digitalWrite(PIN_PH, (val < 0.f) ? LOW : HIGH); // Reverse or Forward
  analogWrite(PIN_EN, (uint16_t)fabsf(val * PWM_MAG));
}

void encoderIndexISR() 
{
  if (USE_EXT_ENC || !releaseForUse)  // reset encoder per cycle causes tiny audible glitch with AS5074D ABI
  {                                    // but not with external encoder
    motorEncoder.write(0); // Zero the encoder position on index pulse
    encCnt = 0;            // Zero the tracked position
    encIndex++;
  }
}
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
void loop() 
{
  static int      operStep     = 0;
  static uint32_t magPoleTime  = 0;
  static uint32_t lastDebugMs  = 0;

  switch (operStep)
  {
    case 0:
      if (USE_EXT_ENC)      
        Serial.println("Position from external encoder");
      else
        Serial.println("Position from AS5074D");

      Serial.print("ABI resolution ");
      Serial.println(ENC_REZ);
      Serial.print("ABI quad resolution ");
      Serial.println(ENC_QUAD_REZ);
      Serial.print("Calibration resolution ");
      Serial.println(CAL_ENC_REZ);

      Serial.println("Index search");
      releaseForUse = 0;
      enableDrv     = HIGH;
      dirSign       = 1.0f;
      operStep      = (encIndex >= 0) ? 1 : 2;
      slewFreqHz    = uStepPerTurn * .1;  // 10 seconds for complete revolution
      break;

    case 1:
      // On index - move away from it
      Serial.println("On index, moving off index");
      operStep++;
      break;

    case 2:
      // Initialization - find encoder index
      if (encIndex >= 0)        // Ensure index is found
      {
        slewFreqHz  = 0.f;
        magPoleTime = millis();
        Serial.println("Found index, moving to magnetic pole");
        operStep++;
      }
      break;

    case 3:
      // Force rotor to one pole
      cmdDeg = 0.;
      if ((millis() - magPoleTime) > 2000)
      {
        Serial.print("Magnetic pole found at ");
        if (USE_EXT_ENC)
          Serial.print(encDeg);
        else
          Serial.print(magDec);
        Serial.println(" deg");

        Serial.println("Proceeding to position sensor calibration");

        for (int i = 0; i < CAL_CNT; i++) encCal[i].deg = (float)i * 360.f/(float)CAL_CNT;
        encOffset  = encDeg;
        encCalRun  = CAL_LEARN;
        slewFreqHz = (float)uStepPerTurn / 20.f; // 20 seconds per turn - calibration run
        operStep++;
      }
      break;

    case 4:
      // Sweep full cycle for mapping (non linearity LUT)
      if (encCalRun == CAL_DONE)
      {
        releaseForUse = 1;
        operStep      = 10;  // Initialization completed
        IdReq         = 1.0f * DIRECT_CURR;  // Lower direct current to reduce heating and noise
        buildSegments();     // Compute slope/intercepts for magnetic sensor linearization table
        fitFourier();        // Fit data to fourrier order
        Serial.println("Position sensor calibration completed");
        Serial.println("Driver released to host control");
      }
      break;

    case 10:
      // Send shaft position to host (no Rx expected)
      uint8_t data[10] = {0};
      short Enc = -(int)(motDeg * (float)0x3fff / 360.f);// Convert to match Servo57D 14 bits

      data[0] = 0x10 | ((Enc>>12) & 0xf);  // MSB
      data[1] = 0x20 | ((Enc>> 8) & 0xf);
      data[2] = 0x30 | ((Enc>> 4) & 0xf);
      data[3] = 0x40 | ((Enc>> 0) & 0xf);  // LSB
      rs485Write((const uint8_t *)&data, 4);
      break;
  }

  if ((USE_EXT_ENC == 0) && !magBusy && magStat)
  {
    magBusy = 1;
    //uint16_t err  = AS5047_Read(AS5047_ERRFL);
    //uint16_t stat = AS5047_Read(AS5047_STATUS);
    //uint16_t diag = AS5047_Read(AS5047_DIAG);
    magBusy = 0;
    // TODO: log errors
  }

  if ((operStep > 4) && (millis() - lastDebugMs >= 100) && 1)
  {
    sTab(" isrTmUs=",       isrTmUs);
//  sTab(" isrCount=",      isrCount);
//  sTab(" enableDrv=",     enableDrv);
//  sTab(" dirSign=",       dirSign);
//  sTab(" freqMeasureHz=", freqMeasureHz);
//  sTab(" fMax=",          fMax);
//  sTab(" fMin=",          fMin);
//  sTab(" slewFreqHz=",    slewFreqHz);
//  sTab(" commRad=",       commRad);
//  sTab(" magRad=",        magRad);
//  sTab(" Va=",            Va);
//  sTab(" Vb=",            Vb);
//  sTab(" Vd=",            Vd);
//  sTab(" Vq=",            Vq);
//  sTab(" Ia=",            Ia);
//  sTab(" Ib=",            Ib);
//  sTab(" Id=",            Id);
//  sTab(" Iq=",            Iq);
//  sTab(" IqDem=",         IqDem);
//  sTab(" IaPol=",         IaPol);
//  sTab(" IbPol=",         IbPol);
//  sTab(" slewRate=",      slewRate);
//  sTab(" encVel=",        encVel);
//  sTab(" encVel2=",       encVel2);
    sTab(" motorVel=",      motorVel);
    sTab(" cmdDeg=",        cmdDeg);
//  sTab(" calTrg=",        calTrg);
//  sTab(" magDeg=",        magDeg);
//  sTab(" magDec=",        magDec);
    sTab(" encDeg=",        encDeg);
//  sTab(" encCnt=",        encCnt);
//  sTab(" magDec=",        magDec);
//  sTab(" magStat=",       magStat);
//  sTab(" phaseAdv=",      phaseAdv);
    sTab(" pE=",            pE);
    sTab(" pEI=",           pEI);
//  sTab(" vE=",            vE);
//  sTab(" vEI=",           vEI);
//  sTab(" vqE=",           vqE);
//  sTab(" vqEI=",          vqEI);

    Serial.println();

    lastDebugMs = millis();
  }

  // --- Host step loss detection ---
  if (!hostTimedOut && ((millis() - lastHostStepTime) > LOSS_TIMEOUT_MS)) hostTimedOut = true;

  delay(20);
}

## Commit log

2026-03-04 Name change, multiple improvements
    File name change, D-Q currents, PI servo, glass disk encoder input (2500ppr), etc
2026-03-08 work in progress
    Work in progress.... FOC d-q velocity computation...
2026-03-16 implemented FOC further
    - no longer using sine LUT, using sin/cos math
    - no longer using 8 step
    - using direct mode at low RPM with position servo only
    - using FOC for high speeds with velocity servo only
    - using period counter for encoder > motor speed
    [SineDriveByPololuDRV8874.ino]
2026-03-27 Update SineDriveByPololuDRV8874.ino
    Working glitches from transitions across 0<>360 boundaries
    [SineDriveByPololuDRV8874.ino]
2026-03-29 Update SineDriveByPololuDRV8874.ino
    At sideral rates ( near 0.25 RPM), reduced per ISR iteration slew to prevent glitches from occasional incorrect freq signal
    [SineDriveByPololuDRV8874.ino]
2026-03-29 Update SineDriveByPololuDRV8874.ino
    Corrected diff limit on low RPM
    [SineDriveByPololuDRV8874.ino]
2026-05-12 Nema23 back end card mount,
    Supports back end magnet or quad encoder
    [TeensyDRV8874-In2_Cu (1)-B_Cu.gbl, TeensyDRV8874-In2_Cu (1)-B_Mask.gbs, TeensyDRV8874-In2_Cu (1)-B_Silkscreen.gbo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]
2026-05-12 Enhance ReadMe with board mounting details
    Added additional information about board mounting options for encoders.
2026-06-07 Update after fully functional PCB and motor + software
    [Nema23DRV8824.scad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]
2026-06-07 Update ReadMe with additional image and content
    Added an image link for the DRV8874 stepper motor driver.
2026-06-19 OpenScad housing for RPi Zero 2W and laser
    [OV9281CamRPiZero2W.scad, OV9281CamRPiZero2WBase.stl, OV9281CamRPiZero2WCover.stl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]
2026-06-19 File in wrong repo - removing
    [OV9281CamRPiZero2W.scad, OV9281CamRPiZero2WBase.stl, OV9281CamRPiZero2WCover.stl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]
2026-06-20 Worked external encoder version
    ..and made code more easily switching between AS5074D and external encoder. Added standalone housing for when external encoder is used
    [Nema23DRV8824 StandAlone.scad, Nema23DRV8824 StandAloneBase.stl, Nema23DRV8824 StandAloneCover.stl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]
2026-06-22 Further working direct mode servo
